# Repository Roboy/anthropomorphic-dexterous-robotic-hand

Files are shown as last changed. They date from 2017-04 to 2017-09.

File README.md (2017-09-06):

# anthropomorphic-hand
This repo contains design files for fusion 360 as well as a description how to set up the robotic hand (prototype1 & 2).

The human hand has a very delicate and complex structure. This allows muscles and joints in the hand a great range of movement and precision. The goal of this work is to build a tendon driven anthropomorphic robotic hand, which is able to closely mimic the human hand. Because of the inherent complexity of human hand, biomimetic anthropomorphic hand inevitably involves lots of compromises while maintaining a human-ish form factor. The hand for Roboy is designed based on the general idea of Roboy, whose limbs are all driven with motors using tendons. Due to the complexity of the human hand, lots of simplifications (like reducing the degree of freedom and integrated mechanical joints) are required.

## Current challenges & scope for the future work:
The prototype 1 was only a test prototype for Roboy and the prototype 2 is more compact with a better design in comparison to the prototype 1.
To make the robotic hand adaptable to the Roboy 2.0 hand-arm system, the following points were considered: 

        - The design have to look more human like. 
        - The new tendon routing have to support the precision of the fingers. 
        - Since the space for the motors is limited, the new robotic hand should have a reasonable degree of freedom. 
        - A Simulation of a mathematical model for the tendon driven hand have to be created.
        - Another servo motor (with more power) has to be selected in order to increase the gripping force of the hand. 
        - To control the wrist a sensor system is necessary (sensor angle measurement).

### Prototype 1
The prototype 1 was developed independently from Roboy to test the design of five tendon driven fingers with the servo system driven by 25 motors. 

#### Useful links
- The documentation of the Prototype 1 can be found here: https://devanthro.atlassian.net/wiki/display/R2M/Anthropomorphic+hand+for+Roboy
- The CAD files of the Prototype 1 can be found here: https://github.com/Roboy/anthropomorphic-dexterous-robotic-hand/tree/master/CAD/Prototype1
- The documentation of the coding can be found here: https://github.com/Roboy/anthropomorphic-dexterous-robotic-hand/tree/master/Programming/Prototype1

### Prototype 2
The second prototype was developed in order to adapt it into Roboy 2.0 (SS 2017). The second prototype has 20 servo motors which will be integrated in Roboy´s new arm (Documentation: https://devanthro.atlassian.net/wiki/display/R2M/Arms). The new design of Roboy´s hand will be more humanlike and an additional wrist was developed. The new tendon routing improved the precision in comparison to the old robotic hand. Furthermore, a sensor system on the wrist will be implemented.

#### Useful links
- The documentation of the Prototype 2 can be found here: https://devanthro.atlassian.net/wiki/display/R2M/Anthropomorphic+hand+for+Roboy
- The CAD files of the Prototype 2 can be found here: https://github.com/Roboy/anthropomorphic-dexterous-robotic-hand/tree/master/CAD/Prototype2
- The documentation of the coding can be found here: https://github.com/Roboy/anthropomorphic-dexterous-robotic-hand/tree/master/Programming/Prototype2

### Pictures of the prototype 1 & 2

#### Prototype 1
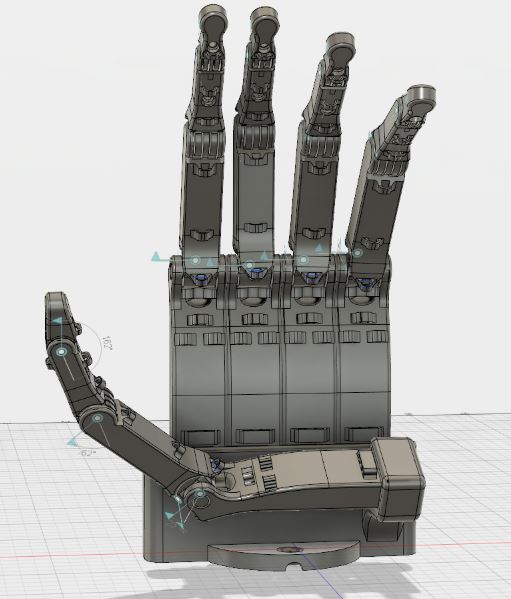
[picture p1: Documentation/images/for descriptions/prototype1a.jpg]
prototype1a


#### Prototype 2
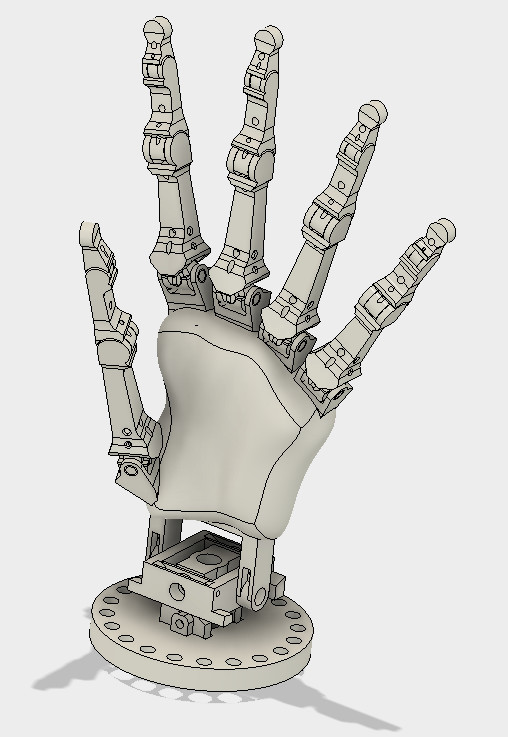
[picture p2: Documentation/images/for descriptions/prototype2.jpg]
prototype2


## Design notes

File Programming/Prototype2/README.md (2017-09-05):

# Anthropomorphic-hand-prototype2
This repo contains design files for fusion 360 as well as a description how to set up the Arduino and the Adafruit motorboard for the hand (prototype2).

The documentation of the Prototype 2 can be found here: https://devanthro.atlassian.net/wiki/display/R2M/Anthropomorphic+hand+for+Roboy

prototype2

## Hardware
For the prototype2 the following hardware is used:
```
- Genuino 101 (power supply via laptop)
- 2 Adafruit 16-Channel 12-bit PWM Servo Driver,
- A power supply (5V, 10A) for the motor boards.
- DC jack 2,1 x 5,5 mm adapter with screw terminal for the power supply
- 20 Hitec Midi-Servo HS-81 Analog-Servo
- 3D printed hand including the wrist.
```
# Building from source
The following instructions guide you through the process of building this repo from source.

## Install the Arduino Software

To program the Arduino board you need the Arduino environment.
Download Arduino: From the software page. (https://www.arduino.cc/en/Main/Software)

Linux note: For help getting the Arduino IDE running on Debian, please see the FAQ ("How can I run the Arduino IDE under Linux?").

Mac OS X note: After downloading the IDE, run the macosx_setup.command. It corrects permission on a few files for use with the serial port and will prompt you for your password. You may need to reboot after running this script.

## Connect the board

See also instruction here: https://www.arduino.cc/en/main/howto

If you're using a serial board, power the board with an external power supply (6 to 25 volts DC, with the core of the connector positive). Connect the board to a serial port on your computer.

On the USB boards, the power source is selected by the jumper between the USB and power plugs. To power the board from the USB port (good for controlling low power devices like LEDs), place the jumper on the two pins closest to the USB plug. To power the board from an external power supply (needed for motors and other high current devices), place the jumper on the two pins closest to the power plug. Either way, connect the board to a USB port on your computer. On Windows, the Add New Hardware wizard will open; tell it you want to specify the location to search for drivers and point to the folder containing the USB drivers you unzipped in the previous step.

The power LED should go on.
 
 ## Read more about the Arduino IDE

In case of troubleshooting
https://www.arduino.cc/en/Guide/Environment?from=Main.Environment

# Adafruit 16-Channel Servo Driver with Arduino
## Hooking it Up: Connecting the motorboard to the Arduino

Driving servo motors with the Arduino Servo library is pretty easy, but each one consumes a
precious pin - not to mention some Arduino processing power. The Adafruit 16-Channel 12-bit
PWM/Servo Driver will drive up to 16 servos over I2C with only 2 pins. The on-board PWM
controller will drive all 16 channels simultaneously with no additional Arduino processing
overhead. What's more, you can chain up to 62 of them to control up to 992 servos - all with the
same 2 pins!
The Adafruit PWM/Servo Driver is the perfect solution for any project that requires a lot of
servos.

The PWM/Servo Driver uses I2C so it take only 4 wires to connect to your Arduino:

### Genuino 101
```
+5v -> VCC (this is power for the BREAKOUT only, NOT the servo power!)
GND -> GND
SDA -> SDA
SCL -> SCL
```
### "Classic" Arduino wiring:
```
+5v -> VCC (this is power for the BREAKOUT only, NOT the servo power!)
GND -> GND
Analog 4 -> SDA
Analog 5 -> SCL
```
### Older Mega wiring:
```
+5v -> VCC (this is power for the BREAKOUT only, NOT the servo power!)
GND -> GND
Digital 20 -> SDA
Digital 21 -> SCL
```
### R3 and later Arduino wiring (Uno, Mega & Leonardo):
```
(These boards have dedicated SDA & SCL pins on the header nearest the USB connector)
+5v -> VCC (this is power for the BREAKOUT only, NOT the servo power!)
GND -> GND
SDA -> SDA
SCL -> SCL
```
The VCC pin is just power for the chip itself. If you want to connect servos or LEDs that use the
V+ pins, you MUST connect the V+ pin as well. The V+ pin can be as high as 6V even if VCC is
3.3V (the chip is 5V safe). We suggest connecting power through the blue terminal block since it
is polarity protected.

## Power for the Servos

Most servos are designed to run on about 5 or 6v. Keep in mind that a lot of servos moving at
the same time (particularly large powerful ones) will need a lot of current. Even micro servos
will draw several hundred mA when moving. Some High-torque servos will draw more than 1A
each under load.
Good power choices are:
5v 2A switching power supply (http://adafru.it/276)
5v 10A switching power supply (http://adafru.it/658)
4xAA Battery Holder (http://adafru.it/830) - 6v with Alkaline cells. 4.8v with NiMH
rechargeable cells.
4.8 or 6v Rechargeable RC battery packs from a hobby store.
It is not a good idea to use the Arduino 5v pin to power your servos. Electrical noise and
'brownouts' from excess current draw can cause your Arduino to act erratically, reset and/or
overheat.
We use the following power for 20 servos: 5A, 10A (https://www.amazon.de/gp/product/B00KETLBAU/ref=oh_aui_detailpage_o00_s00?ie=UTF8&psc=1)

## Connecting a Servo motor

We use the SG90 TowerPro Servos (http://www.micropik.com/PDF/SG90Servo.pdf).
Most servos come with a standard 3-pin female connector that will plug directly into the headers
on the Servo Driver. Be sure to align the plug with the ground wire (usually black or brown) with
the bottom row and the signal wire (usually yellow or white) on the top.

A single servo should be plugged into the PWM #0 port, the first port. You should see the servo
sweep back and forth over approximately 180 degrees. 

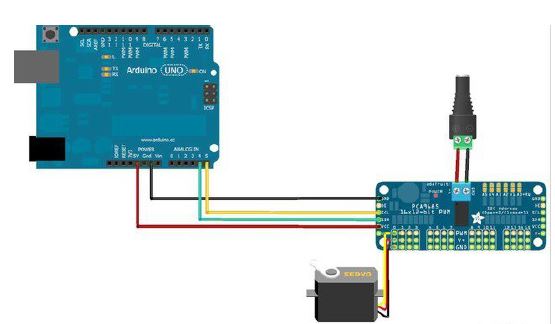
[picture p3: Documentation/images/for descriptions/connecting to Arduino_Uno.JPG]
connecting to Arduino_Uno


Up to 16 servos can be attached to one board.

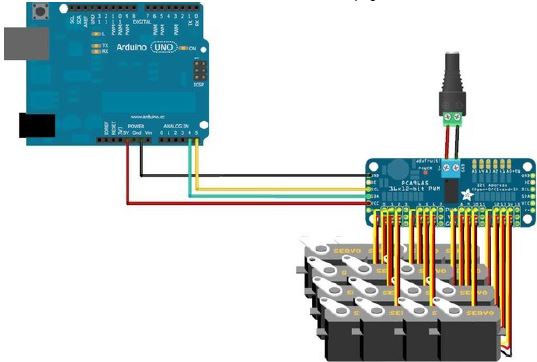
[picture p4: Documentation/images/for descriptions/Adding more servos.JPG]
Adding more servos


## Chaining drivers
Multiple Drivers (up to 62) can be chained to control still more servos. With headers at both
ends of the board, the wiring is as simple as connecting a 6-pin parallel
cable (http://adafru.it/206) from one board to the next. In our case we use 2 motor boards for controlling 20 servo motors. 

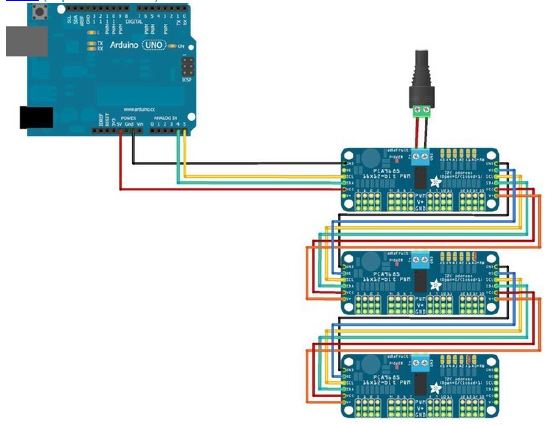
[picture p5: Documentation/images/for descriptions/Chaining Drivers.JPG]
Chaining Drivers


# Using the Adafruit Library

Since the PWM Servo Driver is controlled over I2C, its super easy to use with any microcontroller or microcomputer. 

## Download the library from Github

Start by downloading the library from the GitHub repository (http://adafru.it/aQl) You can do that
by visiting the github repo and manually downloading or, easier, just click this button to
download the zip
Download Adafruit PWM/Servo Library
http://adafru.it/cDw
Rename the uncompressed folder Adafruit_PWMServoDriver and check that the
Adafruit_PWMServoDriver folder contains Adafruit_PWMServoDriver.cpp and
Adafruit_PWMServoDriver.h
Place the Adafruit_PWMServoDriver library folder your arduinosketchfolder/libraries/ folder.
You may need to create the libraries subfolder if its your first library. Restart the IDE.
There is also a great tutorial on how to install the library:
http://learn.adafruit.com/adafruit-all-about-arduino-libraries-install-use (http://adafru.it/aYM)

# Upload the Code
Upload the Code for the movement of the 5 Fingers: "sketch_prototype2.ino" to the Arduino. 
https://github.com/Roboy/anthropomorphic-dexterous-robotic-hand/blob/master/Programming/Prototype2/sketch_prototype2

### Verify/Compile 
Checks your sketch for errors compiling it; it will report memory usage for code and variables in the console area.
### Upload 
Compiles and loads the binary file onto the configured board through the configured Port.

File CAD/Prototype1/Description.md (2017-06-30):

## Software Autodesk Fusion 360

### Helpful links
- You can find the Installation guide for Fusion 360 here: https://knowledge.autodesk.com/support/fusion-360/troubleshooting/caas/sfdcarticles/sfdcarticles/How-does-Fusion-360-get-installed.html
- You can find the Reference Manual here: http://help.autodesk.com/view/fusion360/ENU/?guid=GUID-A92A4B10-3781-4925-94C6-47DA85A4F65A
- Support Page Fusion 360: https://www.autodesk.com/products/fusion-360/support

### Software constraints
- The CAD files were developed on Windows 8, there Autodesk Fusion 360 runs for sure.
- Fusion 360 is well established within the Roboy Mechatronics Team.

## Hardware
For the prototype1 the following hardware is used:
- Robotic hand (3D printed)
- Genuino 101 (power supply via laptop)
- 2 Adafruit 16-Channel 12-bit PWM Servo Driver, 
- A power supply (5V, 10A) for the motorboards
- 20 servo motors: Hitec Midi-Servo HS-81 Analog-Servo

See also the documentation: https://devanthro.atlassian.net/wiki/display/R2M/Roboy+hand

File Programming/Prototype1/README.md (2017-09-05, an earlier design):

# Anthropomorphic-hand-prototype1
This repo contains design files for fusion 360 as well as a description how to set up the Arduino and the Adafruit motorboard for the hand (prototype1).

The documentation of the Prototype 1 can be found here: https://devanthro.atlassian.net/wiki/display/R2M/Anthropomorphic+hand+for+Roboy

prototype1a

## Hardware
For the prototype1 the following hardware is used:
```
- Robotic hand (3D printed)
- Genuino 101 (power supply via laptop)
- 2 Adafruit 16-Channel 12-bit PWM Servo Driver, 
- A power supply (5V, 10A) for the motorboards
- DC jack 2,1 x 5,5 mm adapter with screw terminal for the power supply
- 25 servos (TowerPro, Micro Servo SG90).
```
# Building from source
The following instructions guide you through the process of building this repo from source.

## Install the Arduino Software

To program the Arduino board you need the Arduino environment.
Download Arduino: From the software page. (https://www.arduino.cc/en/Main/Software)

Linux note: For help getting the Arduino IDE running on Debian, please see the FAQ ("How can I run the Arduino IDE under Linux?").

Mac OS X note: After downloading the IDE, run the macosx_setup.command. It corrects permission on a few files for use with the serial port and will prompt you for your password. You may need to reboot after running this script.

## Connect the board

See also instruction here: https://www.arduino.cc/en/main/howto

If you're using a serial board, power the board with an external power supply (6 to 25 volts DC, with the core of the connector positive). Connect the board to a serial port on your computer.

On the USB boards, the power source is selected by the jumper between the USB and power plugs. To power the board from the USB port (good for controlling low power devices like LEDs), place the jumper on the two pins closest to the USB plug. To power the board from an external power supply (needed for motors and other high current devices), place the jumper on the two pins closest to the power plug. Either way, connect the board to a USB port on your computer. On Windows, the Add New Hardware wizard will open; tell it you want to specify the location to search for drivers and point to the folder containing the USB drivers you unzipped in the previous step.

The power LED should go on.
 
 ## Read more about the Arduino IDE

In case of troubleshooting
https://www.arduino.cc/en/Guide/Environment?from=Main.Environment

# Adafruit 16-Channel Servo Driver with Arduino
## Hooking it Up: Connecting the motorboard to the Arduino

Driving servo motors with the Arduino Servo library is pretty easy, but each one consumes a
precious pin - not to mention some Arduino processing power. The Adafruit 16-Channel 12-bit
PWM/Servo Driver will drive up to 16 servos over I2C with only 2 pins. The on-board PWM
controller will drive all 16 channels simultaneously with no additional Arduino processing
overhead. What's more, you can chain up to 62 of them to control up to 992 servos - all with the
same 2 pins!
The Adafruit PWM/Servo Driver is the perfect solution for any project that requires a lot of
servos.

The PWM/Servo Driver uses I2C so it take only 4 wires to connect to your Arduino:

### Genuino 101
```
+5v -> VCC (this is power for the BREAKOUT only, NOT the servo power!)
GND -> GND
SDA -> SDA
SCL -> SCL
```
### "Classic" Arduino wiring:
```
+5v -> VCC (this is power for the BREAKOUT only, NOT the servo power!)
GND -> GND
Analog 4 -> SDA
Analog 5 -> SCL
```
### Older Mega wiring:
```
+5v -> VCC (this is power for the BREAKOUT only, NOT the servo power!)
GND -> GND
Digital 20 -> SDA
Digital 21 -> SCL
```
### R3 and later Arduino wiring (Uno, Mega & Leonardo):
```
(These boards have dedicated SDA & SCL pins on the header nearest the USB connector)
+5v -> VCC (this is power for the BREAKOUT only, NOT the servo power!)
GND -> GND
SDA -> SDA
SCL -> SCL
```
The VCC pin is just power for the chip itself. If you want to connect servos or LEDs that use the
V+ pins, you MUST connect the V+ pin as well. The V+ pin can be as high as 6V even if VCC is
3.3V (the chip is 5V safe). We suggest connecting power through the blue terminal block since it
is polarity protected.

## Power for the Servos

Most servos are designed to run on about 5 or 6v. Keep in mind that a lot of servos moving at
the same time (particularly large powerful ones) will need a lot of current. Even micro servos
will draw several hundred mA when moving. Some High-torque servos will draw more than 1A
each under load.
Good power choices are:
5v 2A switching power supply (http://adafru.it/276)
5v 10A switching power supply (http://adafru.it/658)
4xAA Battery Holder (http://adafru.it/830) - 6v with Alkaline cells. 4.8v with NiMH
rechargeable cells.
4.8 or 6v Rechargeable RC battery packs from a hobby store.
It is not a good idea to use the Arduino 5v pin to power your servos. Electrical noise and
'brownouts' from excess current draw can cause your Arduino to act erratically, reset and/or
overheat.
We use the following power for 25 servos: 5A, 10A (https://www.amazon.de/gp/product/B00KETLBAU/ref=oh_aui_detailpage_o00_s00?ie=UTF8&psc=1)

## Connecting a Servo motor

We use the SG90 TowerPro Servos (http://www.micropik.com/PDF/SG90Servo.pdf).
Most servos come with a standard 3-pin female connector that will plug directly into the headers
on the Servo Driver. Be sure to align the plug with the ground wire (usually black or brown) with
the bottom row and the signal wire (usually yellow or white) on the top.

A single servo should be plugged into the PWM #0 port, the first port. You should see the servo
sweep back and forth over approximately 180 degrees. 

connecting to Arduino_Uno

Up to 16 servos can be attached to one board.

Adding more servos

## Chaining drivers
Multiple Drivers (up to 62) can be chained to control still more servos. With headers at both
ends of the board, the wiring is as simple as connecting a 6-pin parallel
cable (http://adafru.it/206) from one board to the next. In our case we use 2 motor boards for controlling 25 servo motors. 

Chaining Drivers

# Using the Adafruit Library

Since the PWM Servo Driver is controlled over I2C, its super easy to use with any microcontroller or microcomputer. 

## Download the library from Github

Start by downloading the library from the GitHub repository (http://adafru.it/aQl) You can do that
by visiting the github repo and manually downloading or, easier, just click this button to
download the zip
Download Adafruit PWM/Servo Library
http://adafru.it/cDw
Rename the uncompressed folder Adafruit_PWMServoDriver and check that the
Adafruit_PWMServoDriver folder contains Adafruit_PWMServoDriver.cpp and
Adafruit_PWMServoDriver.h
Place the Adafruit_PWMServoDriver library folder your arduinosketchfolder/libraries/ folder.
You may need to create the libraries subfolder if its your first library. Restart the IDE.
There is also a great tutorial on how to install the library:
http://learn.adafruit.com/adafruit-all-about-arduino-libraries-install-use (http://adafru.it/aYM)

# Upload the Code
Upload the Code for the movement of the 5 Fingers: "first_prototype_5fingers.ino" to the Arduino. 
https://github.com/Roboy/anthropomorphic-dexterous-robotic-hand/blob/master/Programming/Prototype1/first_prototype_5fingers.ino

### Verify/Compile 
Checks your sketch for errors compiling it; it will report memory usage for code and variables in the console area.
### Upload 
Compiles and loads the binary file onto the configured board through the configured Port.

# Experimental setup
In the picture below you can see the experimental setup of the prototype 1. Further description of the experimental setup can be found on the following link: https://devanthro.atlassian.net/wiki/display/R2M/Anthropomorphic+hand+for+Roboy

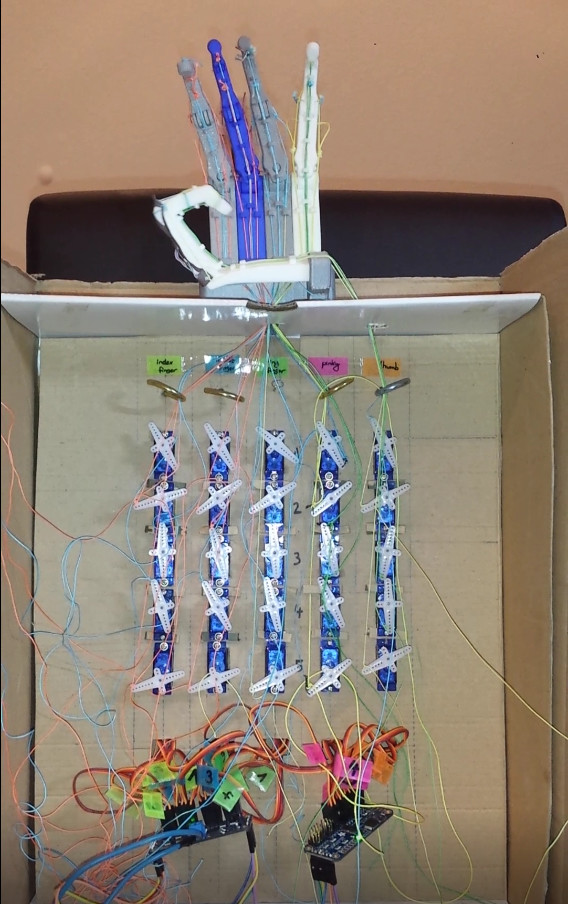
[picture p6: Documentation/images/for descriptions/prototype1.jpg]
prototype1


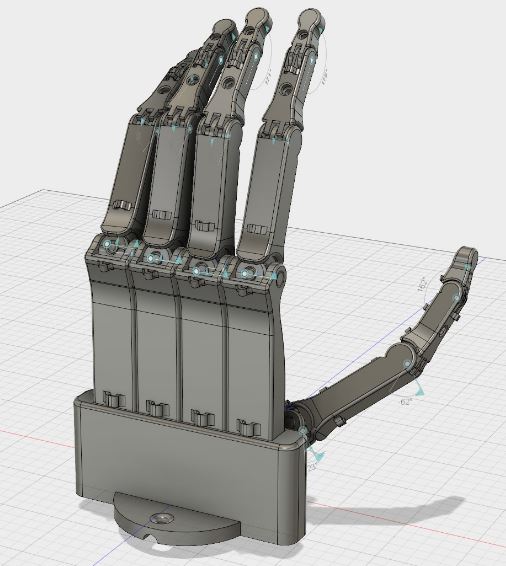
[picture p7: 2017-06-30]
Documentation/images/for descriptions/prototype1b.jpg

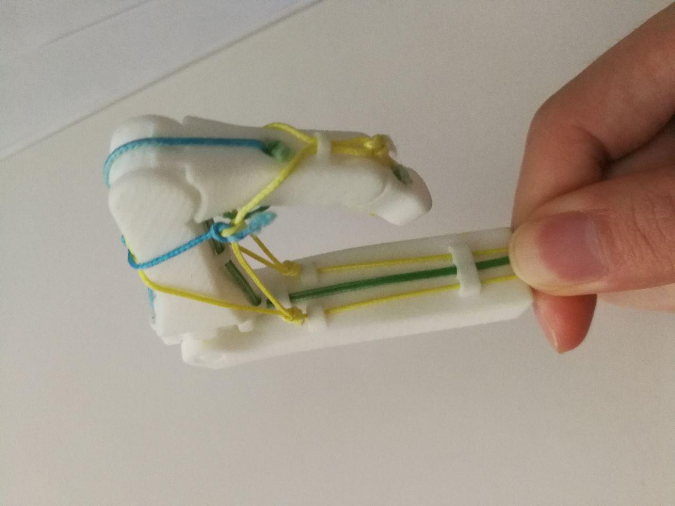
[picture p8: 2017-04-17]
Documentation/images/development of one finger/tendon-fixation_photo_2017-03-04_07-48-29 (5).jpg

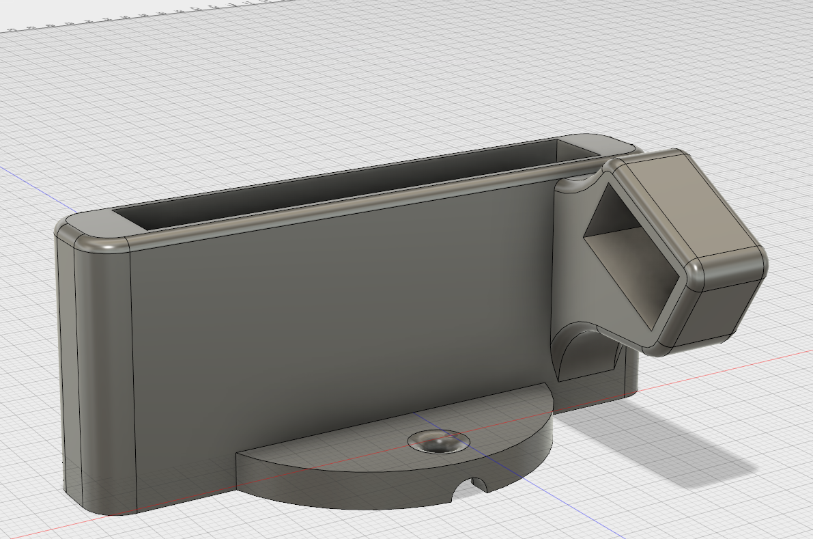
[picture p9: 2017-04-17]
Documentation/images/first prototype/Basis.PNG

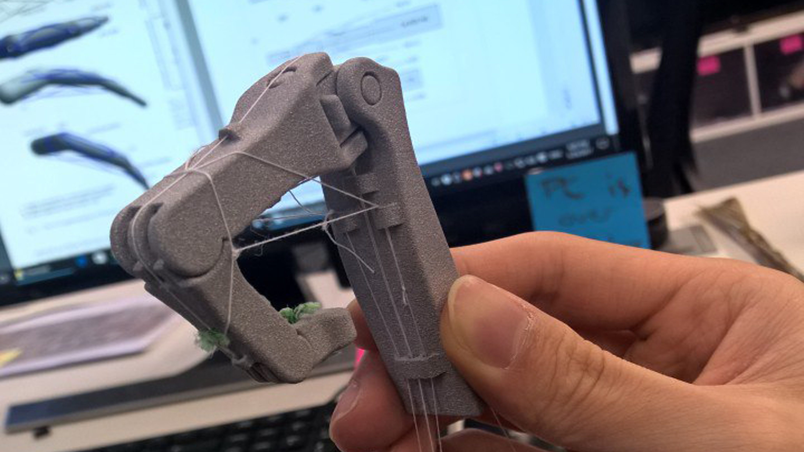
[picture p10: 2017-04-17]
Documentation/images/development of one finger/20170125_131247b.jpg

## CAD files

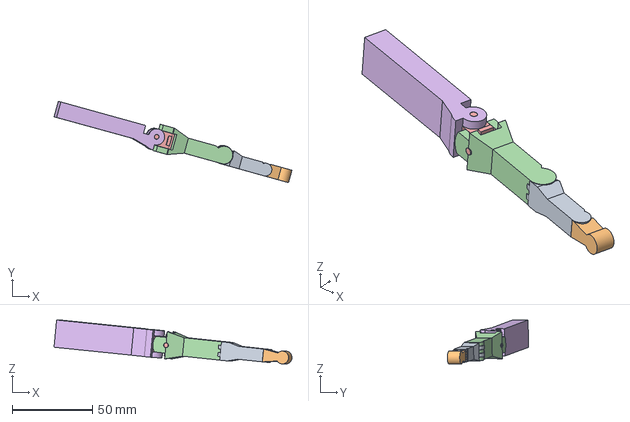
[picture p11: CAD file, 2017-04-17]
CAD/Prototype1/finger/Finger_Assembly v8.iges
148.0 x 50.6 x 27.3 mm

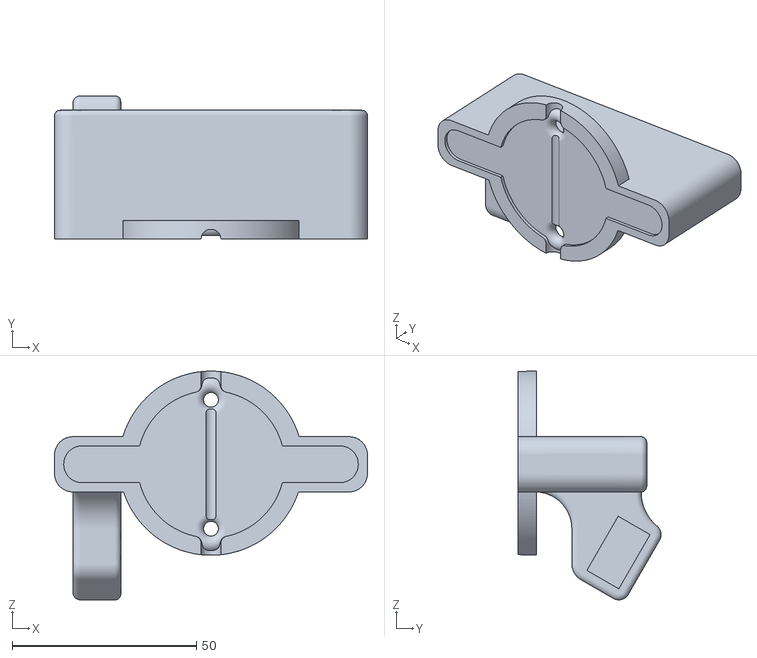
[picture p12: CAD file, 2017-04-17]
CAD/Prototype1/finger holder -hand palm/Basis v2.stl
85.0 x 38.9 x 62.1

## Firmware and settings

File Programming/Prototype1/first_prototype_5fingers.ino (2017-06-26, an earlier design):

#include <Wire.h>
#include <Adafruit_PWMServoDriver.h>

//600 is the 'maximum' pulse length count (out of 4096)
int pos1 = 600; // indexfinger 
int pos2 = 600; // middlefinger
int pos3 = 600; // ringfinger
int pos4 = 600; // pinky
int pos5 = 600; // thumb
int pos123 = 600; // for the movements flexion & stretch


////////////////////////////////////////////////////////
///////////////////    CONSTANTS    ///////////////////
////////////////////////////////////////////////////////
const int UNTERES_LIMIT = 170; // this value depends on the adjustment of the servos
const int OBERES_LIMIT = 580; // this value depends on the adjustment of the servos
const int SCHRITTWEITE = 10; // setting up the step size of the servos

// There are two different adresses for the two Adafruit motor boards: pwm & pwm2
Adafruit_PWMServoDriver pwm = Adafruit_PWMServoDriver(0x40);
Adafruit_PWMServoDriver pwm2 = Adafruit_PWMServoDriver(0x41);

void setup() {
  // put your setup code here, to run once:
  Serial.begin(9600);
  Serial.println("movement of the roboy hand");
  pwm.begin();
  pwm2.begin();

  // Servos run at ~50 Hz updates
  pwm.setPWMFreq(50);  
  pwm2.setPWMFreq(50); 
  yield();
}

////////////////////////////////////////////////////////
//////////////////    FLEXION_ALL    ///////////////////
////////////////////////////////////////////////////////

void strecken_beugen_alle_gleichzeitig(){
  while( pos123 <= OBERES_LIMIT )
  {
    // indexfinger motors: 10, 11, 12, 13, 14 (pwm board)
    // motor10: stretch, motor11: tilt left, motor12: finger flexion, motor13: fingertip flexion, motor14: tilt right
    pwm.setPWM(10, 0, pos123);   
    pwm.setPWM(11, 0, 600);  
    pwm.setPWM(12, 0, pos123);
    pwm.setPWM(13, 0, pos123);
    pwm.setPWM(14, 0, 600);
    
    // middlefinger motors: 5, 6, 7, 8, 9 (pwm board)
    // motor5: stretch, motor6: tilt left, motor7: finger flexion, motor8: fingertip flexion, motor9: tilt right
    pwm.setPWM(5, 0, pos123);   
    pwm.setPWM(6, 0, 600);  
    pwm.setPWM(7, 0, pos123);
    pwm.setPWM(8, 0, pos123);
    pwm.setPWM(9, 0, 600);

    // ringfinger motors: 0, 1, 2, 3, 4 (pwm board)
    // motor0: stretch, motor1: tilt left, motor2: finger flexion, motor3: fingertip flexion, motor4: tilt right
    pwm.setPWM(0, 0, pos123);   
    pwm.setPWM(1, 0, 600);  
    pwm.setPWM(2, 0, pos123);
    pwm.setPWM(3, 0, pos123);
    pwm.setPWM(4, 0, 600);

    // pinky motors: 5, 6, 7, 8, 9 (pwm2 board)
    // motor5: stretch, motor6: tilt left, motor7: finger flexion, motor8: fingertip flexion, motor9: tilt right
    pwm2.setPWM(5, 0, pos123);   
    pwm2.setPWM(6, 0, 600);  
    pwm2.setPWM(7, 0, pos123);
    pwm2.setPWM(8, 0, pos123);
    pwm2.setPWM(9, 0, 600);

    // thumb motors: 0, 1, 2, 3, 4 (pwm2 board)
    // motor0: stretch, motor1: tilt left, motor2: finger flexion, motor3: fingertip flexion, motor4: tilt right
    pwm2.setPWM(0, 0, pos123);   
    pwm2.setPWM(1, 0, 600);  
    pwm2.setPWM(2, 0, pos123);
    pwm2.setPWM(3, 0, pos123);
    pwm2.setPWM(4, 0, 600);
    
    Serial.println("Position beugen alle:");
    Serial.println(pos123);
                pos123+=SCHRITTWEITE; 
       }
}


void strecken_beugen_indexfinger(){

do
   {
    // indexfinger motors: 10, 11, 12, 13, 14 (pwm board)
    // motor10: stretch, motor11: tilt left, motor12: finger flexion, motor13: fingertip flexion, motor14: tilt right
    pwm.setPWM(10, 0, pos1);   
    pwm.setPWM(11, 0, 600);  
    pwm.setPWM(12, 0, pos1);
    pwm.setPWM(13, 0, pos1);
    pwm.setPWM(14, 0, 600);
    Serial.println("Position beugen indexfinger:");
    Serial.println(pos1);
    pos1+=SCHRITTWEITE;
 
 
//    delay(0.5);
   } while (pos1 <= 580);
}

void strecken_beugen_middlefinger(){

do
   {
    // middlefinger motors: 5, 6, 7, 8, 9 (pwm board)
    // motor5: stretch, motor6: tilt left, motor7: finger flexion, motor8: fingertip flexion, motor9: tilt right
    pwm.setPWM(5, 0, pos2);   
    pwm.setPWM(6, 0, 600);   
    pwm.setPWM(7, 0, pos2);
    pwm.setPWM(8, 0, pos2);
    pwm.setPWM(9, 0, 600);
    Serial.println("Position beugen middlefinger:");
    Serial.println(pos2);
    pos2+=SCHRITTWEITE;
 
 
//    delay(0.5);
   } while (pos2 <= 580);
}


void strecken_beugen_ringfinger(){

do
   {
    // ringfinger motors: 0, 1, 2, 3, 4 (pwm board)
    // motor0: stretch, motor1: tilt left, motor2: finger flexion, motor3: fingertip flexion, motor4: tilt right
    pwm.setPWM(0, 0, pos3);   
    pwm.setPWM(1, 0, 600);  
    pwm.setPWM(2, 0, pos3);
    pwm.setPWM(3, 0, pos3);
    pwm.setPWM(4, 0, 600);
    Serial.println("Position beugen ringfinger:");
    Serial.println(pos3);
    pos3+=SCHRITTWEITE;
 
 
//    delay(0.5);
   } while (pos3 <= 580);
}

void strecken_beugen_pinky(){

do
   {
    // pinky motors: 5, 6, 7, 8, 9 (pwm2 board)
    // motor5: stretch, motor6: tilt left, motor7: finger flexion, motor8: fingertip flexion, motor9: tilt right
    pwm2.setPWM(5, 0, pos4);   
    pwm2.setPWM(6, 0, 600);  
    pwm2.setPWM(7, 0, pos4);
    pwm2.setPWM(8, 0, pos4);
    pwm2.setPWM(9, 0, 600);
    Serial.println("Position beugen pinky:");
    Serial.println(pos4);
    pos4+=SCHRITTWEITE;
 
 
//    delay(0.5);
   } while (pos4 <= 580);
}

void strecken_beugen_thumb(){

do
   {
    // thumb motors: 0, 1, 2, 3, 4 (pwm2 board)
    // motor0: stretch, motor1: tilt left, motor2: finger flexion, motor3: fingertip flexion, motor4: tilt right
    pwm2.setPWM(0, 0, pos5);   
    pwm2.setPWM(1, 0, 600);  
    pwm2.setPWM(2, 0, pos5);
    pwm2.setPWM(3, 0, pos5);
    pwm2.setPWM(4, 0, 600);
    Serial.println("Position beugen thumb:");
    Serial.println(pos5);
    pos5+=SCHRITTWEITE;
 
 
//    delay(0.5);
   } while (pos5 <= 580);
}

////////////////////////////////////////////////////////
//////////////////    STRETCH_ALL    ///////////////////
////////////////////////////////////////////////////////

void beugen_strecken_alle_gleichzeitig(){
  while( pos123 >= UNTERES_LIMIT )
  {
    // indexfinger motors: 10, 11, 12, 13, 14 (pwm board)
    // motor10: stretch, motor11: tilt left, motor12: finger flexion, motor13: fingertip flexion, motor14: tilt right
    pwm.setPWM(10, 0, pos123);   
    pwm.setPWM(11, 0, 600);  
    pwm.setPWM(12, 0, pos123);
    pwm.setPWM(13, 0, pos123);
    pwm.setPWM(14, 0, 600);

    // middlefinger motors: 5, 6, 7, 8, 9 (pwm board)
    // motor5: stretch, motor6: tilt left, motor7: finger flexion, motor8: fingertip flexion, motor9: tilt right
    pwm.setPWM(5, 0, pos123);   
    pwm.setPWM(6, 0, 600);  
    pwm.setPWM(7, 0, pos123);
    pwm.setPWM(8, 0, pos123);
    pwm.setPWM(9, 0, 600);

    // ringfinger motors: 0, 1, 2, 3, 4 (pwm board)
    // motor0: stretch, motor1: tilt left, motor2: finger flexion, motor3: fingertip flexion, motor4: tilt right
    pwm.setPWM(0, 0, pos123);   // ringfinger motors: 0, 1, 2, 3, 4 (pwm board)
    pwm.setPWM(1, 0, 600);  
    pwm.setPWM(2, 0, pos123);
    pwm.setPWM(3, 0, pos123);
    pwm.setPWM(4, 0, 600);

    // pinky motors: 5, 6, 7, 8, 9 (pwm2 board)
    // motor5: stretch, motor6: tilt left, motor7: finger flexion, motor8: fingertip flexion, motor9: tilt right
    pwm2.setPWM(5, 0, pos123);   
    pwm2.setPWM(6, 0, 600);  
    pwm2.setPWM(7, 0, pos123);
    pwm2.setPWM(8, 0, pos123);
    pwm2.setPWM(9, 0, 600);

    // thumb motors: 0, 1, 2, 3, 4 (pwm2 board)
    // motor0: stretch, motor1: tilt left, motor2: finger flexion, motor3: fingertip flexion, motor4: tilt right
    pwm2.setPWM(0, 0, pos123);   
    pwm2.setPWM(1, 0, 600);  
    pwm2.setPWM(2, 0, pos123);
    pwm2.setPWM(3, 0, pos123);
    pwm2.setPWM(4, 0, 600);

    
    Serial.println("Position beugen alle:");
    Serial.println(pos123);
                pos123-=SCHRITTWEITE; 
       }
}


void beugen_strecken_indexfinger(){

do
   {
     // indexfinger motors: 10, 11, 12, 13, 14 (pwm board)
    // motor10: stretch, motor11: tilt left, motor12: finger flexion, motor13: fingertip flexion, motor14: tilt right
    pwm.setPWM(10, 0, pos1);   
    pwm.setPWM(11, 0, 600);  
    pwm.setPWM(12, 0, pos1);
    pwm.setPWM(13, 0, pos1);
    pwm.setPWM(14, 0, 600);
    Serial.println("Position strecken indexfinger:");
    Serial.println(pos1);
    pos1-=SCHRITTWEITE;
 
 
//    delay(0.5);
   } while (pos1 >= 170);
} 

void beugen_strecken_middlefinger(){

do
   {
    // middlefinger motors: 5, 6, 7, 8, 9 (pwm board)
    // motor5: stretch, motor6: tilt left, motor7: finger flexion, motor8: fingertip flexion, motor9: tilt right
    pwm.setPWM(5, 0, pos2);   
    pwm.setPWM(6, 0, 600);  
    pwm.setPWM(7, 0, pos2);
    pwm.setPWM(8, 0, pos2);
    pwm.setPWM(9, 0, 600);
    Serial.println("Position strecken middlefinger:");
    Serial.println(pos2);
    pos2-=20;
 
 
//    delay(0.5);
   } while (pos2 >= 170);
} 


void beugen_strecken_ringfinger(){

do
   {
    // ringfinger motors: 0, 1, 2, 3, 4 (pwm board)
    // motor0: stretch, motor1: tilt left, motor2: finger flexion, motor3: fingertip flexion, motor4: tilt right
    pwm.setPWM(0, 0, pos3);   
    pwm.setPWM(1, 0, 600);  
    pwm.setPWM(2, 0, pos3);
    pwm.setPWM(3, 0, pos3);
    pwm.setPWM(4, 0, 600);
    Serial.println("Position strecken ringfinger:");
    Serial.println(pos3);
    pos3-=SCHRITTWEITE;
 
 
//    delay(0.5);
   } while (pos3 >= 170);
} 

void beugen_strecken_pinky(){

do
   {
    // pinky motors: 5, 6, 7, 8, 9 (pwm2 board)
    // motor5: stretch, motor6: tilt left, motor7: finger flexion, motor8: fingertip flexion, motor9: tilt right
    pwm2.setPWM(5, 0, pos4);   
    pwm2.setPWM(6, 0, 600);  
    pwm2.setPWM(7, 0, pos4);
    pwm2.setPWM(8, 0, pos4);
    pwm2.setPWM(9, 0, 600);
    Serial.println("Position strecken pinky:");
    Serial.println(pos4);
    pos4-=SCHRITTWEITE;
 
 
//    delay(0.5);
   } while (pos4 >= 170);
} 

void beugen_strecken_thumb(){

do
   {
    // thumb motors: 0, 1, 2, 3, 4 (pwm2 board)
    // motor0: stretch, motor1: tilt left, motor2: finger flexion, motor3: fingertip flexion, motor4: tilt right
    pwm2.setPWM(0, 0, pos5);   
    pwm2.setPWM(1, 0, 600);  
    pwm2.setPWM(2, 0, pos5);
    pwm2.setPWM(3, 0, pos5);
    pwm2.setPWM(4, 0, 600);
    Serial.println("Position strecken thumb:");
    Serial.println(pos5);
    pos5-=SCHRITTWEITE;
 
 
//    delay(0.5);
   } while (pos5 >= 170);
} 


void loop() {

beugen_strecken_alle_gleichzeitig(); // movement from flexion to stretch
delay(2000);
strecken_beugen_alle_gleichzeitig(); // movement from stretch to flexion
delay(2000);

// movement stretch, all fingers seperately
beugen_strecken_thumb();
beugen_strecken_indexfinger();
beugen_strecken_middlefinger();
beugen_strecken_ringfinger();
beugen_strecken_pinky();


delay(1000);
// movement flexion, all fingers seperately
strecken_beugen_thumb();
strecken_beugen_indexfinger();
strecken_beugen_middlefinger();
strecken_beugen_ringfinger();
strecken_beugen_pinky();

delay(1000);

}

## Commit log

2017-04-17 Create finger
2017-04-17 Create finger
    2017-04-17
2017-04-17 Create Development of one finger
2017-04-17 Add files via upload
    Controlling the hand with one Genuino 101, two Adafruit 16-Channel 12-bit PWM Servo Driver, a power supply (5V, 10A) and 25 servos (TowerPro, Micro Servo SG90).
    https://devanthro.atlassian.net/wiki/display/DRSU/Roboy+hand
2017-06-26 Rename CAD/finger/Finger_Assembly v8.iges to CAD/Prototype1/finger/Finger_Assembly v8.iges
    [Finger_Assembly v8.iges]
2017-06-26 Create Prototype1
